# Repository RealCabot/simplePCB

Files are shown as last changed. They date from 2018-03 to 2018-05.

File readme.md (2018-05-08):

Arduino shield for CaBot
=============================
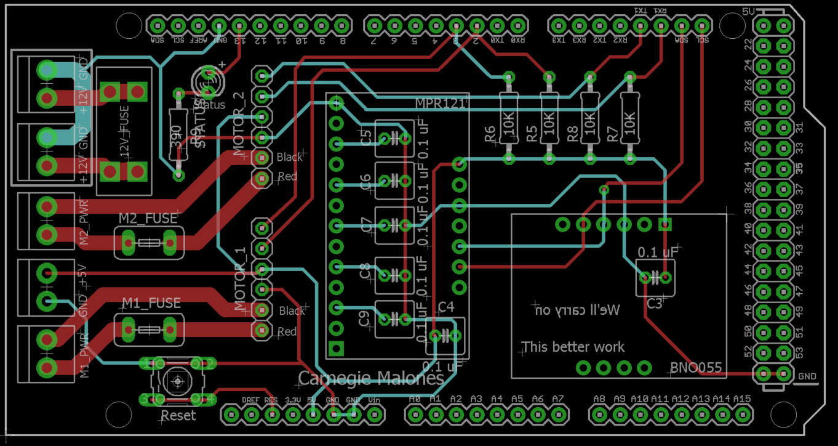
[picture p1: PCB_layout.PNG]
PCB

This shield fits on top of an Arduino Mega. It provides breakouts for the sensors listed below, and fuses to protect the motor driver and motors. The PCB can be connected to a [L298 motor driver](https://solarbotics.com/product/k_cmd/) or a [Sabertooth 2x12 motor driver](https://www.dimensionengineering.com/products/sabertooth2x12).

**Parts list:**
See Excel file: "simple_component_list.xlsx"

**Sensors:**
1) [IMU](https://www.adafruit.com/product/2472)
2) [Touch Sensor](https://www.adafruit.com/product/1982)

**Connections**
1) M1_PWR (motor 1 power) <---> motor 1 positive and negative connections on motor driver
2) M2_PWR (motor 2 power) <---> motor 2 positive and negative connections on motor driver
3) GND (next to 5V) <---> GND on motor driver (this should be common GND)
4) 12V <---> 12V power supply
5) GND (next to 12V) <---> GND of 12V power supply (this should be common GND)
6) Connect Arduino's digital pins to the appropriate inputs on the motor driver. The pins will be different depending on whether you're using the L298 or Sabertooth (RTFM).
**If the motors are running the wrong direction, reverse the polarity**

**Known Issues**

1) The Arduino may disconnect from the laptop when running rosserial. Unfortunately, I don't know what's causing this. This has only happened once during our testing.
2) Current spikes may cause the fuse to blow (CaBot will stop moving). You must replace the 12V fuse if this happens. **You MUST use a 3A fuse with the L298 Motor Driver, otherwise it will burn out.** The Sabertooth can use up to a 20A fuse.

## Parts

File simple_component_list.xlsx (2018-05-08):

Qty | Value | Device | Package | Parts | Description | Lab/own | Ordered | Notes
7 | 0.1 uF | C-US025-050X050 | C025-050X050 | C3, C4, C5, C6, C7, C8, C9 | CAPACITOR, American symbol
4 | 10K | R-US_0207/10 | 0207/10 | R5, R6, R7, R8 | RESISTOR, American symbol
5 | 1X2-3.5MM | 1X2-3.5MM | 1X2-3.5MM | 5V_OUT, 12V_PASS1, 12V_PASS2, M1_PWR, M2_PWR | 3.5mm Terminal block |  |  | Ordered both screw and screwless types
1 | 3568 | 3568 | 3568 | 12V_FUSE | Mini ATC Fuse Holder 20A 500V 1 Circuit Blade PCB |  |  | Ordered both fuse and holder
1 | 390 | R-US_0207/10 | 0207/10 | R9 | RESISTOR, American symbol
1 | ADA_MPR121 | ADA_MPR121 | ADA_MPR121 | MPR121
1 | BNO055 | BNO055 | BNO055 | BNO055
2 | FUSETE5 | FUSETE5 | TE5 | M1_FUSE, M2_FUSE | Fuse |  |  | Order new fuses w/ smaller footprint
1 | MOTOR_1 | PINHD-1X6 | 1X06 | JP1 | PIN HEADER
1 | MOTOR_2 | PINHD-1X6 | 1X06 | JP2 | PIN HEADER
1 | Mega R3 | ARDUINO-MEGAFULL | ARDUINO_MEGA | J2 | Arduino MegaR3 board footprint. Also works for Due.
1 | Reset | 10-XX | B3F-10XX | S2 | OMRON SWITCH
1 | STATUS | LED3MM | LED3MM | LED5 | LED |  |  | Orange LED

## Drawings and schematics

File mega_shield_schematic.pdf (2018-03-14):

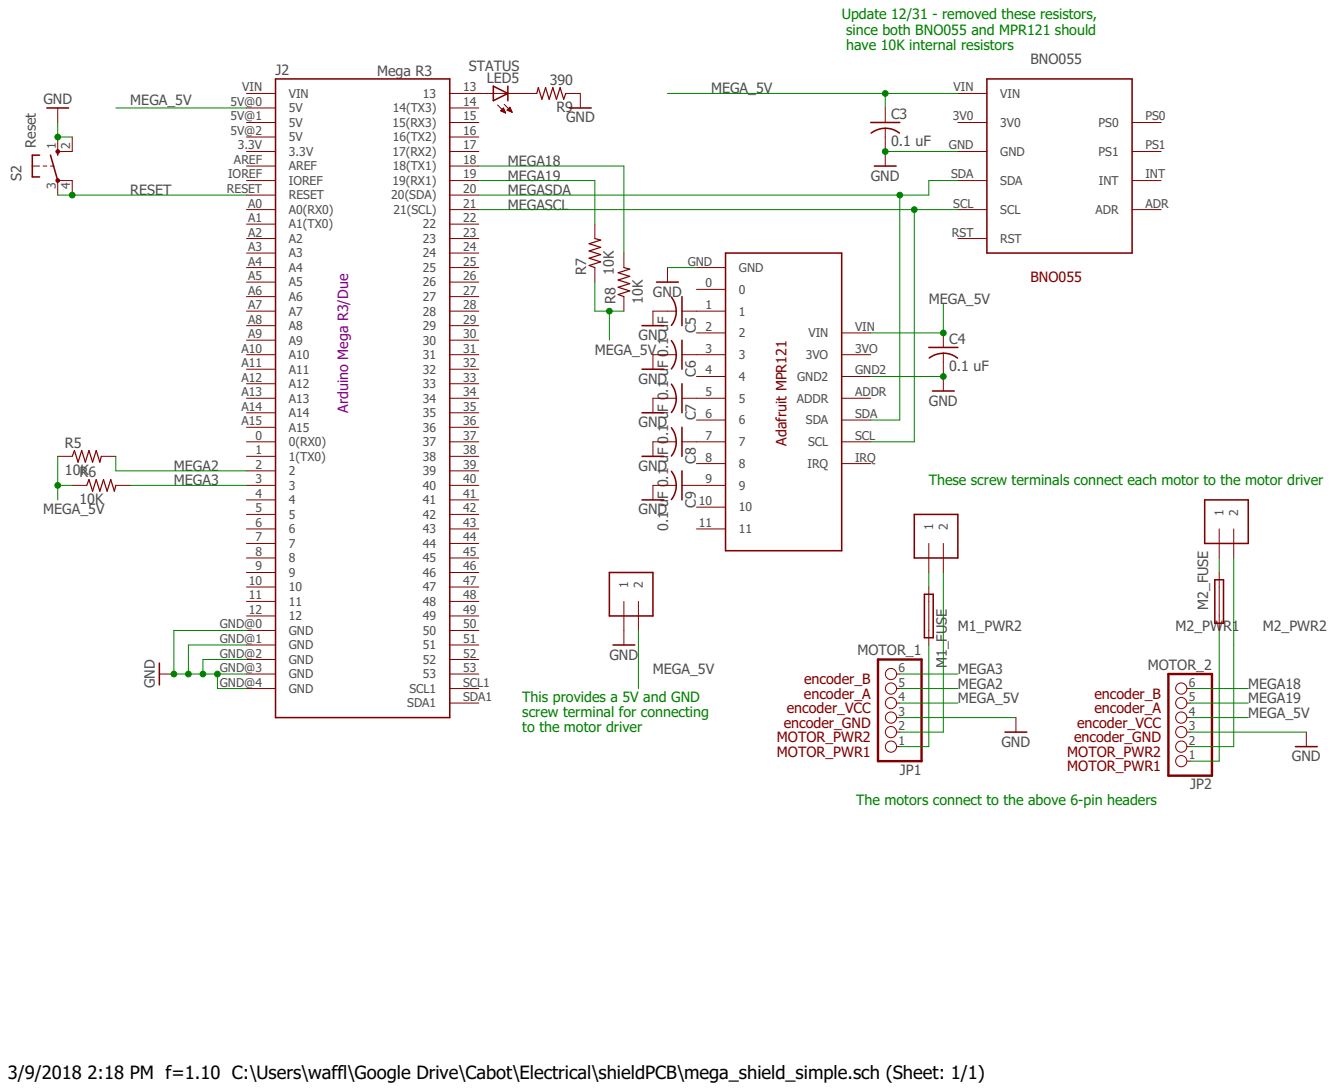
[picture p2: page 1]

Update 12/31 - removed these resistors, since both BNO055 and MPR121 should

Arduino Mega R3/Due Mega R3

A0(RX0) A0 A1(TX0) A1 A2 A2 A3 A3 A4 A4 A5 A5 A6 A6 A7 A7 A8 A8 A9 A9 A10 A10 A11 A11 A12 A12 A13 A13 A14 A14 A15 A15 0(RX0) 0 1(TX0) 1 | MEGASCL

RST

These screw terminals connect each motor to the motor driver

This provides a 5V and GND
screw terminal for connecting
to the motor driver

The motors connect to the above 6-pin headers

3/9/2018 2:18 PM f=1.10 C:\Users\waffl\Google Drive\Cabot\Electrical\shieldPCB\mega_shield_simple.sch (Sheet: 1/1)

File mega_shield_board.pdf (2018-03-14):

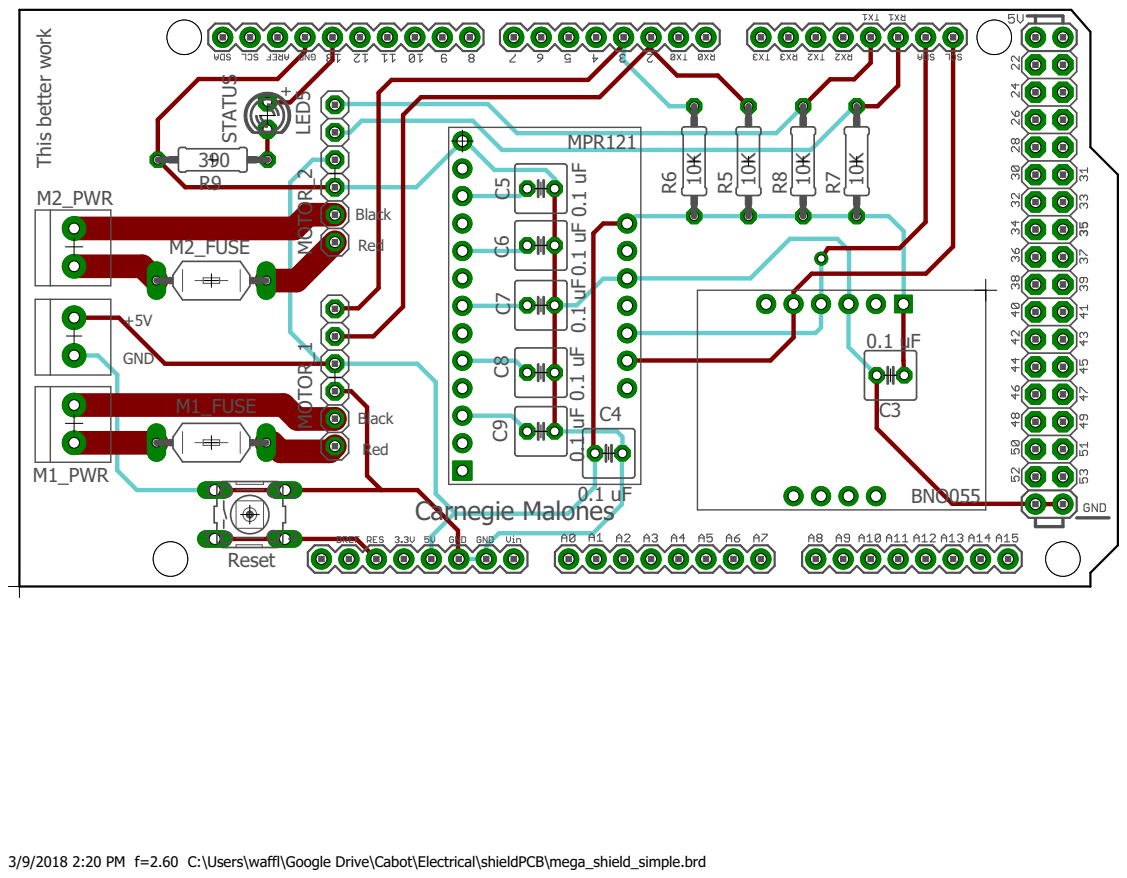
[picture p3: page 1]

3/9/2018 2:20 PM f=2.60 C:\Users\waffl\Google Drive\Cabot\Electrical\shieldPCB\mega_shield_simple.brd

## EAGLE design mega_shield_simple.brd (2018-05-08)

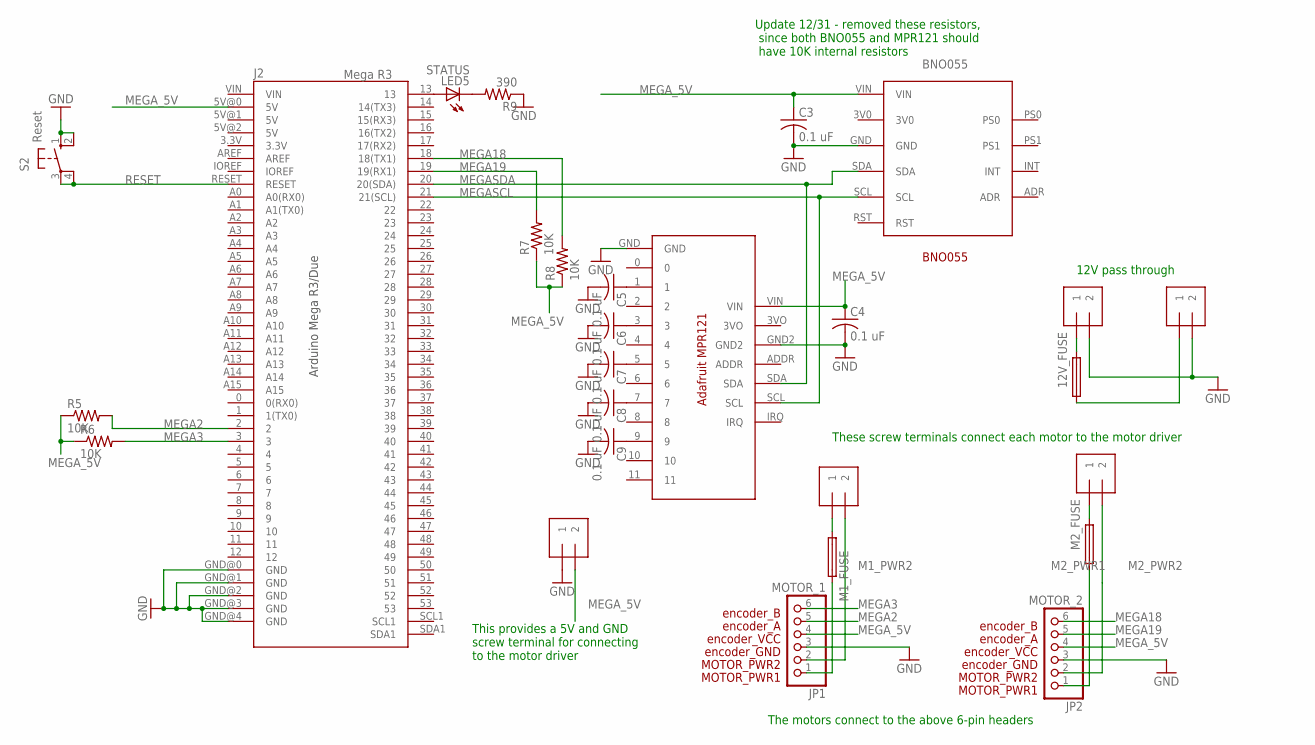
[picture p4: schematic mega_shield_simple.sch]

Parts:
5V_OUT, 12V_PASS1, 12V_PASS2: 1X2-3.5MM
12V_FUSE: 3568
BNO055: BNO055
C3, C4, C5, C6, C7, C8, C9: 0.1 uF; C025-050X050
J2: Mega R3; ARDUINO_MEGA
JP1: MOTOR_1; 1X06
JP2: MOTOR_2; 1X06
LED5: STATUS; LED3MM
M1_FUSE, M2_FUSE: FUSETE5; TE5
M1_PWR, M2_PWR: 1X2-3.5MM
MPR121: ADA_MPR121
R5, R6, R7, R8: 10K; 0207/10
R9: 390; 0207/10
S2: Reset; B3F-10XX

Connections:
12V_PASSTHRU1: 12V_FUSE.1, 12V_FUSE.2 (1), 12V_PASS2.1
12V_PASSTHRU2: 12V_FUSE.3 (2), 12V_FUSE.4 (2), 12V_PASS1.1
GND: 5V_OUT.1, 12V_PASS1.2, 12V_PASS2.2, BNO055.GND, C3.2, C4.2, C5.2, C6.2, C7.2, C8.2, C9.2, J2.GND@0 (GND), J2.GND@1 (GND), J2.GND@2 (GND), J2.GND@3 (GND), J2.GND@4 (GND), JP1.3, JP2.3, MPR121.GND, MPR121.GND2, R9.1, S2.1 (S), S2.2 (S1)
M1_PWR1: JP1.1, M1_FUSE.2
M1_PWR2: JP1.2, M1_PWR.2
M2_PWR1: JP2.1, M2_FUSE.2
M2_PWR2: JP2.2, M2_PWR.2
MEGA2: J2.2, JP1.5, R5.2
MEGA3: J2.3, JP1.6, R6.2
MEGA18: J2.18 (18(TX1)), JP2.6, R8.2
MEGA19: J2.19 (19(RX1)), JP2.5, R7.2
MEGASCL: BNO055.SCL, J2.21 (21(SCL)), MPR121.SCL
MEGASDA: BNO055.SDA, J2.20 (20(SDA)), MPR121.SDA
MEGA_5V: 5V_OUT.2, BNO055.VIN, C3.1, C4.1, J2.5V@0 (5V), JP1.4, JP2.4, MPR121.VIN, R5.1, R6.1, R7.1, R8.1
unnamed: C5.1, MPR121.1
unnamed: C6.1, MPR121.3
unnamed: J2.13, LED5.A
unnamed: LED5.K (C), R9.2
unnamed: C7.1, MPR121.5
unnamed: C8.1, MPR121.7
unnamed: M2_FUSE.1, M2_PWR.1
unnamed: C9.1, MPR121.9
unnamed: M1_FUSE.1, M1_PWR.1
RESET: J2.RESET, S2.3, S2.4 (P1)

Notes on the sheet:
Arduino Mega R3/Due
Update 12/31 - removed these resistors, since both BNO055 and MPR121 should have 10K internal resistors
This provides a 5V and GND screw terminal for connecting to the motor driver
These screw terminals connect each motor to the motor driver
The motors connect to the above 6-pin headers
12V pass through

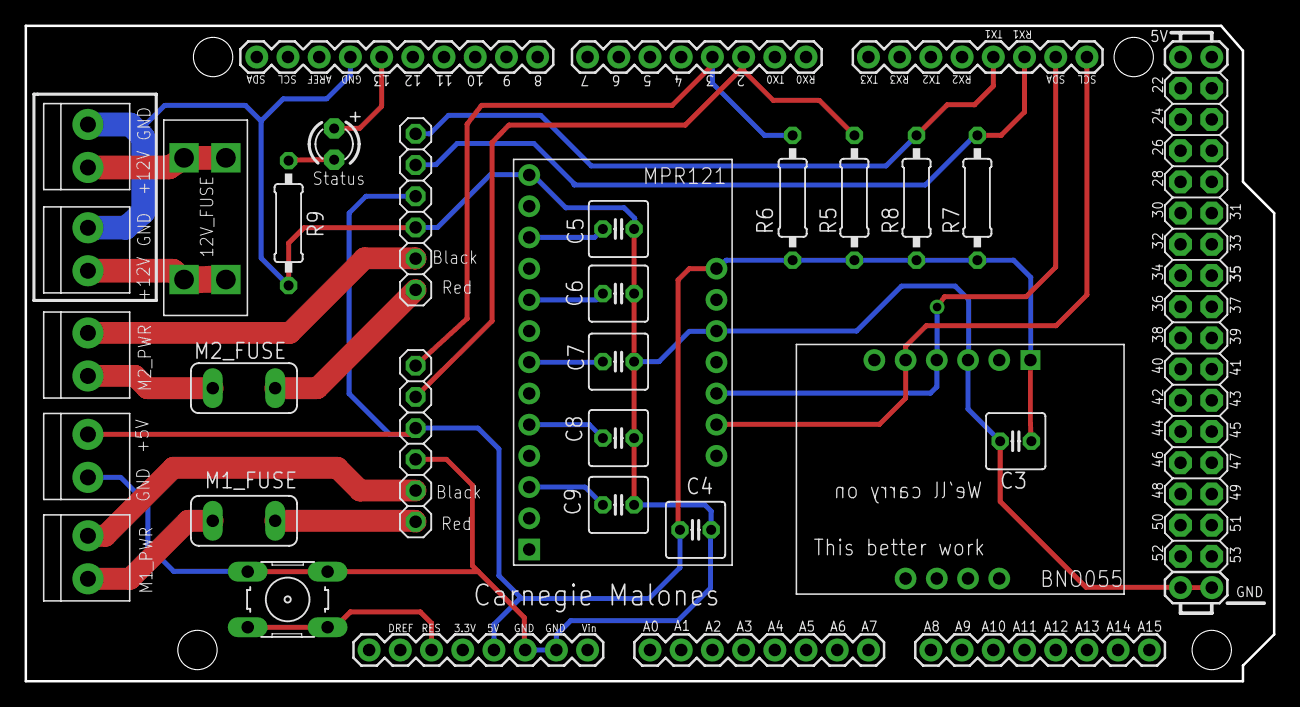
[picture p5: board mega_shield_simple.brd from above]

Board: 2 copper layers, 101.6 x 53.3 mm, 27 parts (0 on the bottom side), 24 nets.

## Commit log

2018-05-08 add fuses to sch and brd files
    [mega_shield_simple.brd, mega_shield_simple.sch]
2018-05-08 Added gerber files
    [component_list_updated.xlsx, simple_component_list.xlsx]
